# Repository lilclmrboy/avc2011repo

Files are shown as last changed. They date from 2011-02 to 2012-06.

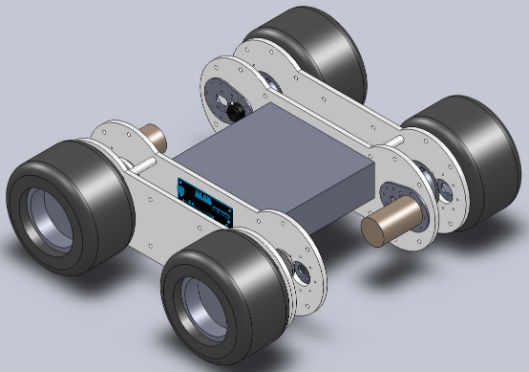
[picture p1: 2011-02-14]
cad/UAV_platform_small.jpg

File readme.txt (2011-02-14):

##########################################################################
# Readme.txt file for AVG2011 project

Download Acroname product sources and integrate the SVN repository. 
Aka, how do I get these files to just work with the download files. 
Launch a terminal session and get to it. 

1.) Move into a directory that you just downloaded the files from Acroname.
2.) Copy the files into your avc2011repo directory

$ cp -Rv acroname/ /Users/you/avc2011rep/source

That should be it. Get working!

##########################################################################
# TEAWare information
# Getting the Stem files ready for deployment to the Stem network

There is a make command to build the project settings for the stem network.

$ make dump

This should create a file to load all the TEAWare onto the Stem network. From the aConsole application:

brainstem> braindump avc2011_dump.dump
wtf

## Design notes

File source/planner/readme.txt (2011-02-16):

Building:
  Currently only builds the release version.
  Requires an acroname directory be a sibling 
  to the examples directory.

Configuration:

Use:

Known Issues:

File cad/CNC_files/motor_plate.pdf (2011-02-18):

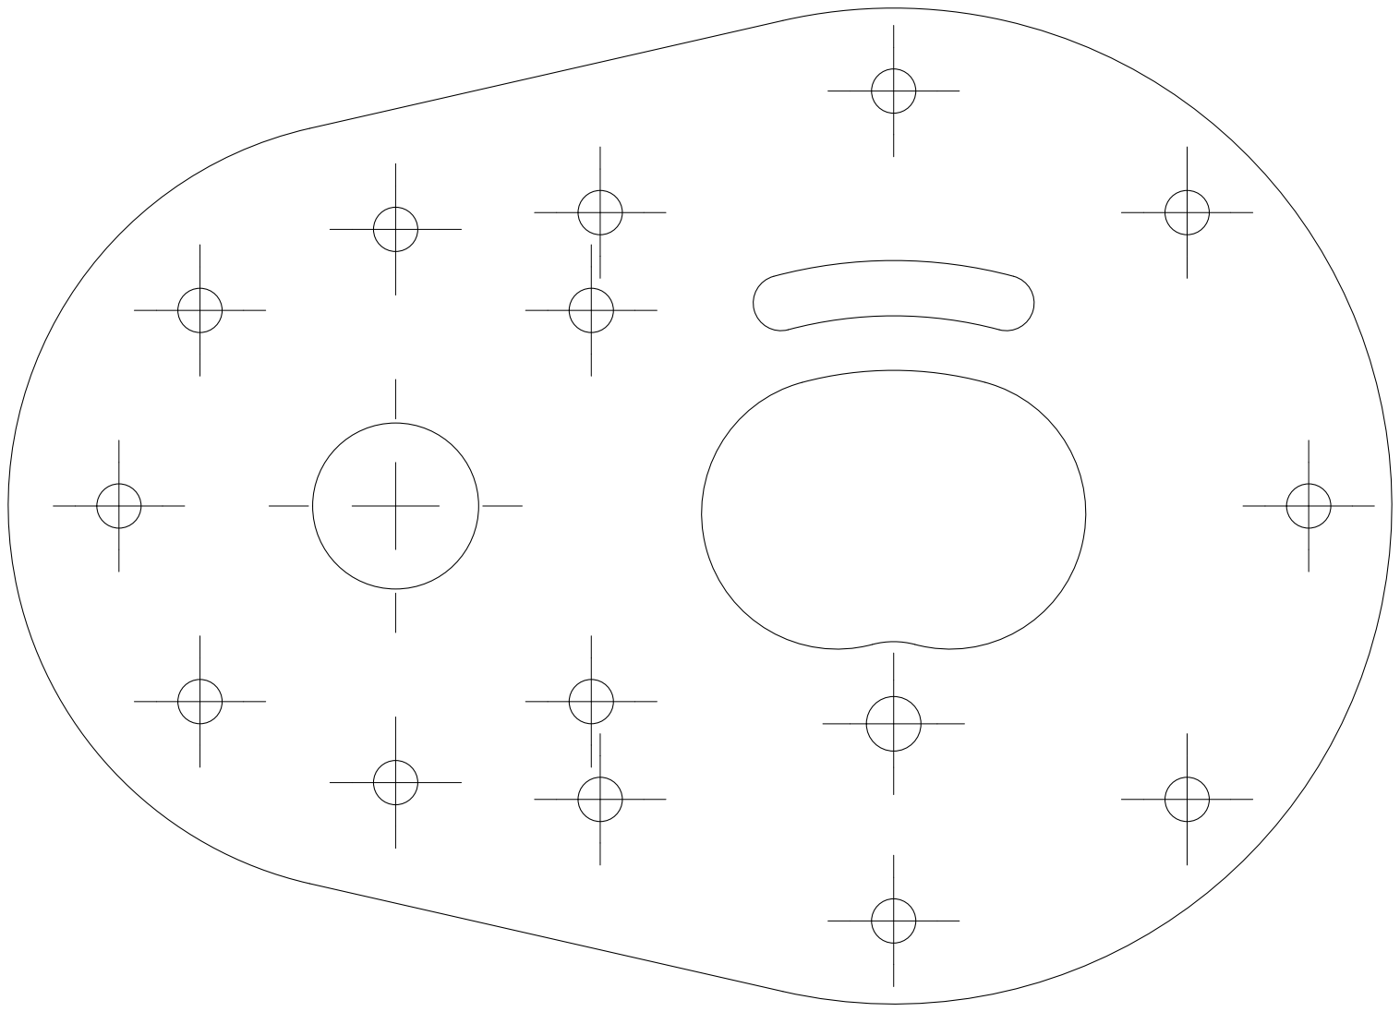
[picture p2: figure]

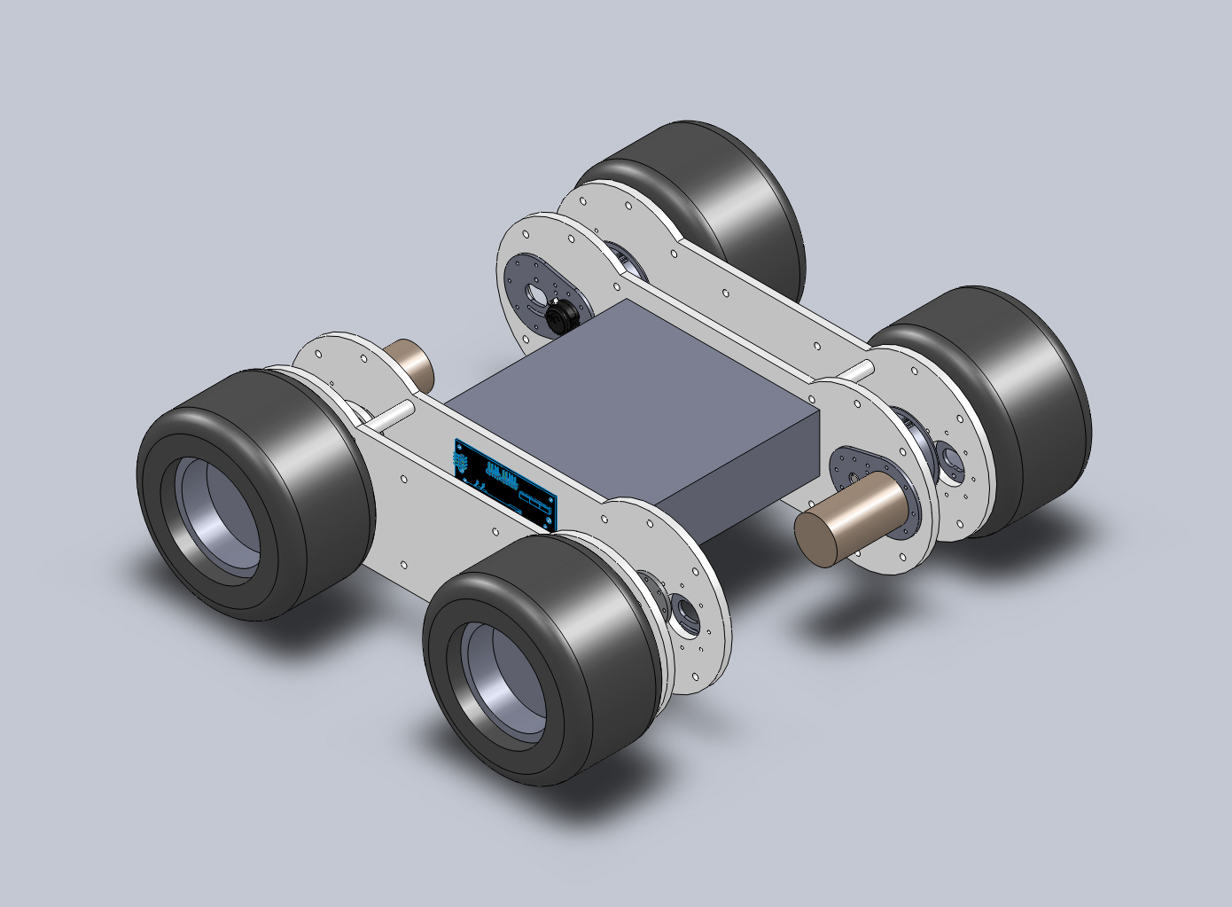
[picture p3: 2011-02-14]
cad/UAV_platform.JPG

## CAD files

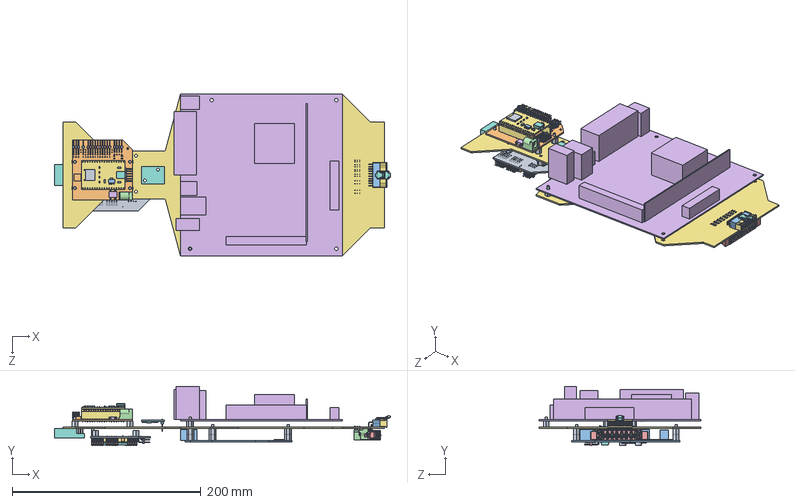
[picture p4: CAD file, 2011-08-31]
cad/avc2012/PCB_Plate_Subsystem.SLDASM
355.8 x 62.8 x 171.4 mm
nylon_standoff_0.25 x 14
BrainStem_Breakout_Eval1
PCONN00009 x 2
PCONN00016
PCONN00027 x 4
TSW-104-08-G-D-RA
SSW-118-01-G-S x 2
TSW-101-08-G-T-RA
TSW-103-08-G-T-RA
Inductor_DR7 x 2
PDIOD00001 x 4
PDIOD00002 x 4
PDIOD00009 x 3
4SMD
BrainStem_USB_Core
USB-minib
DM3D-SF
TSW-118-07-G-S x 2
SOT-223
Capacitor_SMA x 3
LQFP100
PDIOD00013
S08
AR6115
S25-GP2-BRD
PDIOD00003
PCONN00008
PCONN00003
PCONN00012
PCONN00011
PDIPSocket14 x 2
PDIP28
Capacitor_Panasonic_FK_D x 2
PMISC00005
Belkin_F7D1301v1
Samtec-SSW-109-01-G-S
MPSS-08-SR-END
xc-179-xx-x-xx_Crimped x 20
IPD1-XX-D-X-X_6 Position -R
LTC-14-XX-X_-01
T-1S64-XX-X_-09 -RA [IPL1] x 10
T-1S64-XX-X_-10 -RA [IPL1] x 10
IPL1-XX-D-X-XX_No Pol Formula
ced-MPT-XX-RA-XX-XX_8p-SD
ced-T-1M40-XX-X_-02 (.093 PCB) x 8
miniITX
PCB_Plate
R340-CMPS09

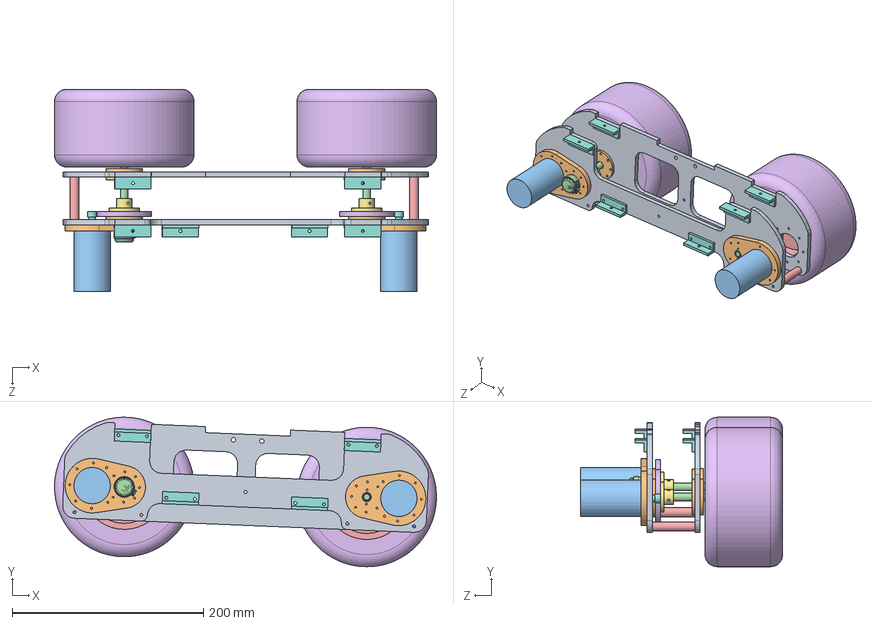
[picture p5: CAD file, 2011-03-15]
cad/Right_Half_Assembly.SLDASM
399.8 x 156.5 x 211.8 mm
Side_Plates2
motor_plate2 x 6
skate_bearing x 4
wheel_shaft x 2
wheel_hub x 2
tire x 2
shaft_hex_connector x 2
angle_supports x 6
Side_Plates2_itx_cutout
motor_plate x 2
titan_550_motor x 2
E4P-X-059-X-D-D-X
spacer x 2
traxxas_32_Pitch_72T_Spur_Gear x 2
traxxas_Spur_Gear_Hub x 2
traxxas_32_Pitch_12T_pINION_Gear x 2

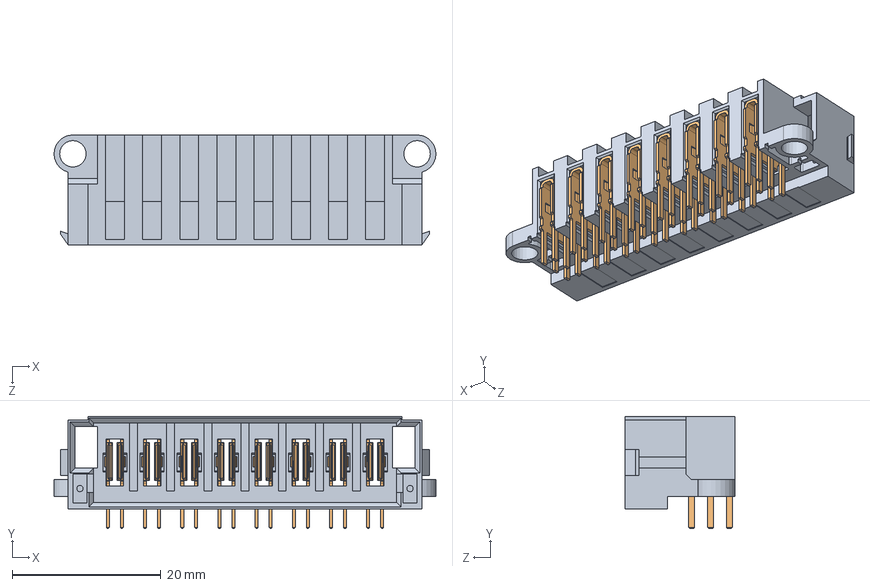
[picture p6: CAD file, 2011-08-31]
cad/avc2012/MPT-08-01-01-X-RA-SD.SLDASM
51.4 x 15.1 x 14.8 mm
ced-MPT-XX-RA-XX-XX_8p-SD
ced-T-1M40-XX-X_-02 (.093 PCB) x 8

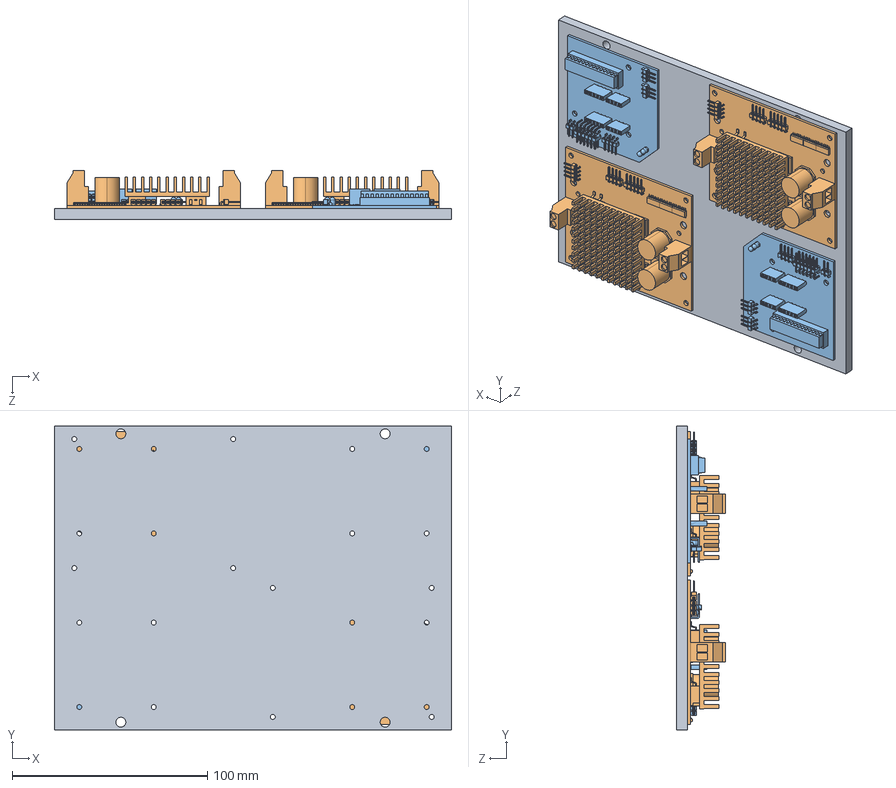
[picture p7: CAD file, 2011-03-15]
cad/bottom_electronics_assembly.SLDASM
203.2 x 155.6 x 25.2 mm
bottom_electronics_plate
S24-15A-30V-HBRIDGE_2010 x 2
S10-MOTO-BRD_2010 x 2

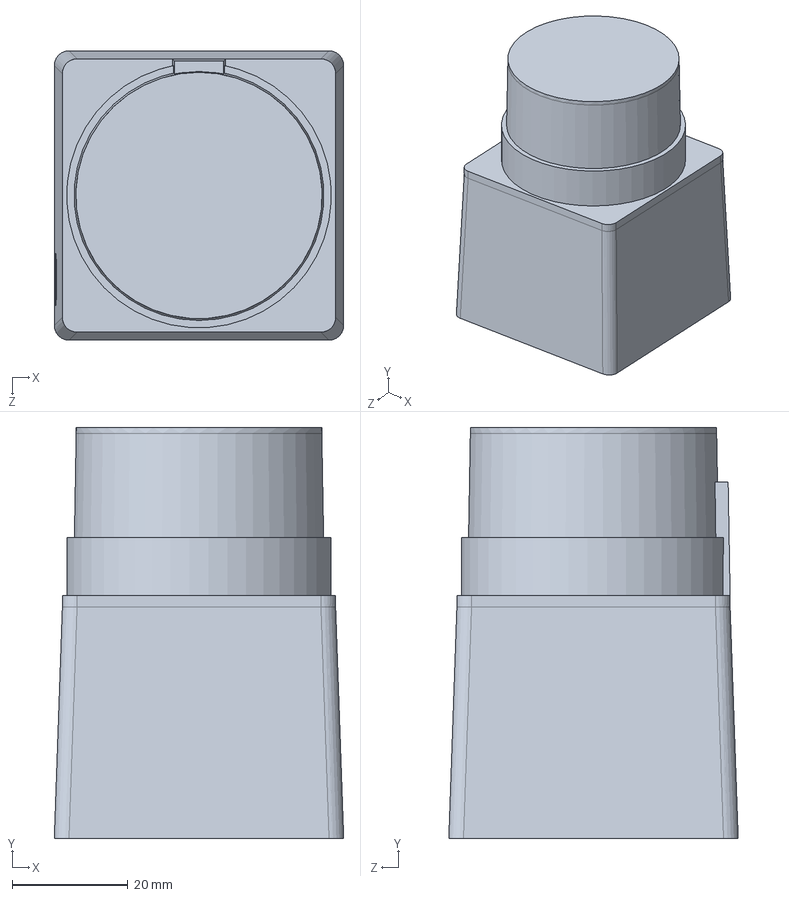
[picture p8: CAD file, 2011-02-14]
cad/SW_2010_files/URG-04LX-UG01_2010.SLDASM
50.0 x 71.0 x 50.0 mm
R325-URG-04LX-UG01
USB-minib

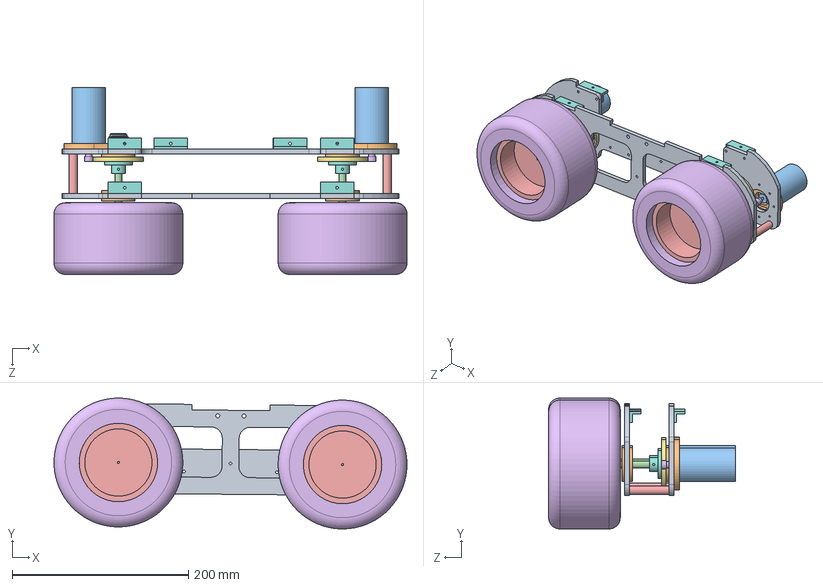
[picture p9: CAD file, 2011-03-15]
cad/Left_Half_Assembly.SLDASM
400.0 x 148.3 x 211.8 mm
Side_Plates2
motor_plate2 x 6
skate_bearing x 4
wheel_shaft x 2
wheel_hub x 2
tire x 2
shaft_hex_connector x 2
angle_supports x 6
Side_Plates2_itx_cutout
motor_plate x 2
titan_550_motor x 2
E4P-X-059-X-D-D-X
spacer x 2
traxxas_32_Pitch_12T_pINION_Gear x 2
traxxas_32_Pitch_72T_Spur_Gear x 2
traxxas_Spur_Gear_Hub x 2

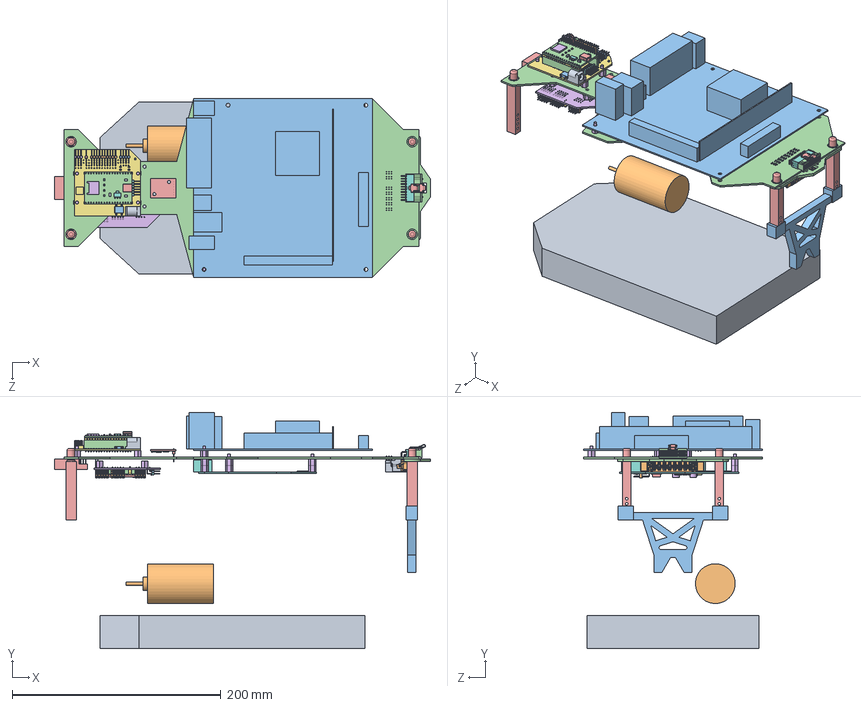
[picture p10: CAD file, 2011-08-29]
cad/avc2012/avc2012.SLDASM
360.5 x 226.6 x 171.4 mm
nylon_standoff_0.25 x 14
BrainStem_Breakout_Eval1
PCONN00009 x 2
PCONN00016
PCONN00027 x 4
TSW-104-08-G-D-RA
SSW-118-01-G-S x 2
TSW-101-08-G-T-RA
TSW-103-08-G-T-RA
Inductor_DR7 x 2
PDIOD00001 x 4
PDIOD00002 x 4
PDIOD00009 x 3
4SMD
BrainStem_USB_Core
USB-minib
DM3D-SF
TSW-118-07-G-S x 2
SOT-223
Capacitor_SMA x 3
LQFP100
PDIOD00013
S08
AR6115
S25-GP2-BRD
PDIOD00003
PCONN00008
PCONN00003
PCONN00012
PCONN00011
PDIPSocket14 x 2
PDIP28
Capacitor_Panasonic_FK_D x 2
PMISC00005
Belkin_F7D1301v1
Samtec-SSW-109-01-G-S
MPSS-08-SR-END
xc-179-xx-x-xx_Crimped x 20
IPD1-XX-D-X-X_6 Position -R
LTC-14-XX-X_-01
T-1S64-XX-X_-09 -RA [IPL1] x 10
T-1S64-XX-X_-10 -RA [IPL1] x 10
IPL1-XX-D-X-XX_No Pol Formula
ced-MPT-XX-RA-XX-XX_8p-SD
ced-T-1M40-XX-X_-02 (.093 PCB) x 8
miniITX
PCB_Plate
R340-CMPS09

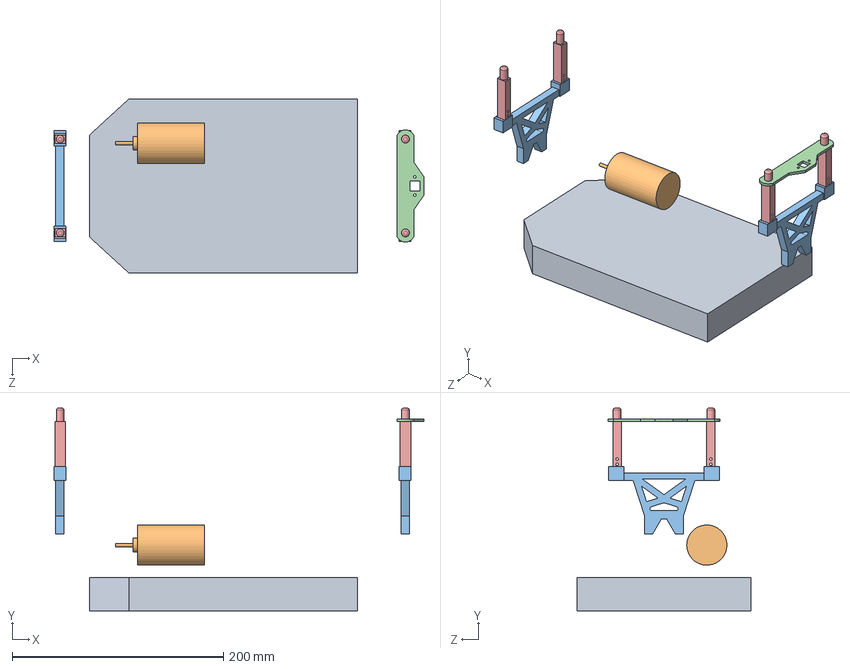
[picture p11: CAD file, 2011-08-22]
cad/avc2012/Traxxas_EMAXX.SLDASM
350.5 x 192.1 x 165.1 mm
Traxxas_EMAXX_Cavity
titan_550_motor
Traxxas_EMAXX_PostBrace x 2
Traxxas_EMAXX_RearPostMount
Traxxas_EMAXX_Post x 4

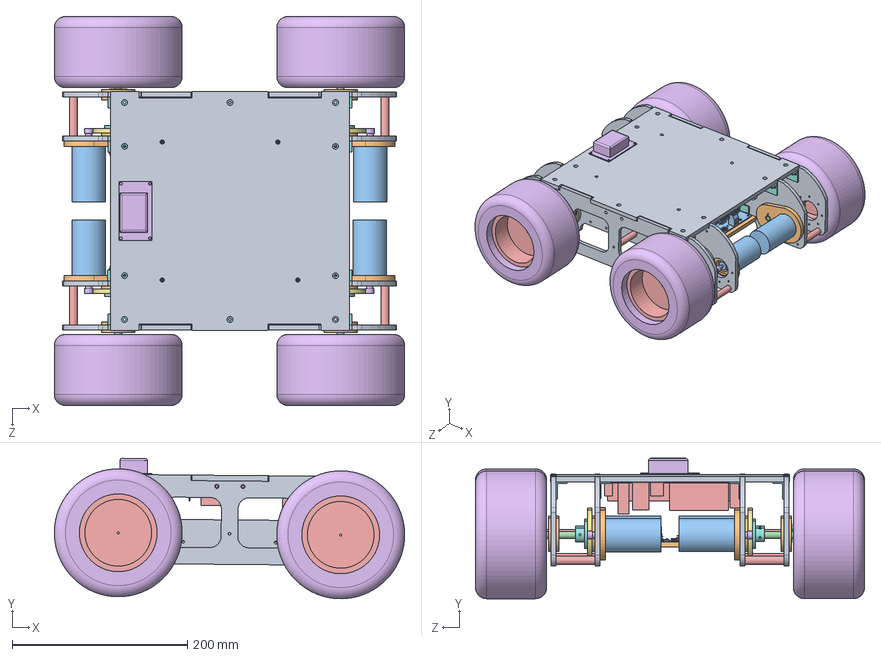
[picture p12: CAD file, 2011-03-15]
cad/UAV_platform3.SLDASM
400.0 x 160.4 x 444.1 mm
Side_Plates2 x 2
motor_plate2 x 12
skate_bearing x 8
wheel_shaft x 4
wheel_hub x 4
tire x 4
shaft_hex_connector x 4
angle_supports x 14
Side_Plates2_itx_cutout x 2
motor_plate x 4
titan_550_motor x 4
E4P-X-059-X-D-D-X x 2
spacer x 6
traxxas_32_Pitch_12T_pINION_Gear x 4
traxxas_32_Pitch_72T_Spur_Gear x 4
traxxas_Spur_Gear_Hub x 4
top_electronic_plate
bottom_electronics_plate
S24-15A-30V-HBRIDGE_2010 x 2
S10-MOTO-BRD_2010 x 2
miniITX
DS-GPMu_2010

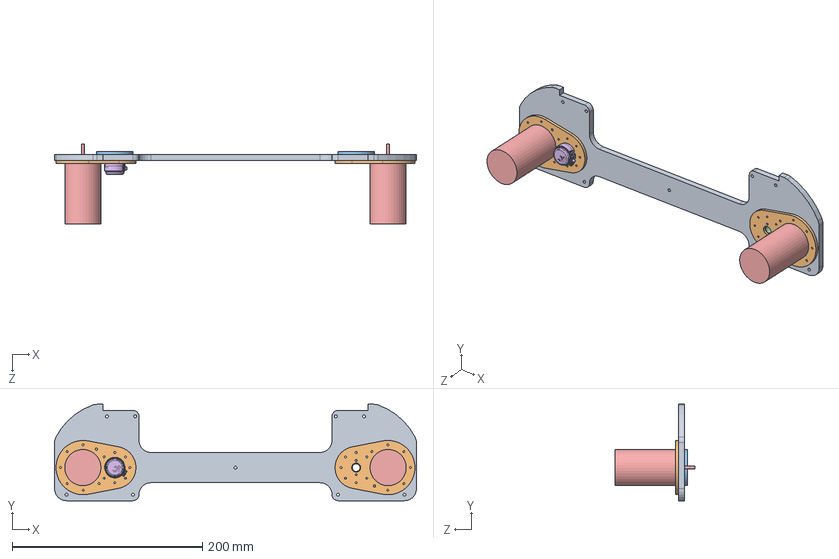
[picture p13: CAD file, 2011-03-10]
cad/Right_Side_Plate_Assembly.SLDASM
381.0 x 101.6 x 84.1 mm
Side_Plates2_itx_cutout
motor_plate x 2
motor_plate2 x 2
skate_bearing x 2
titan_550_motor x 2
E4P-X-059-X-D-D-X

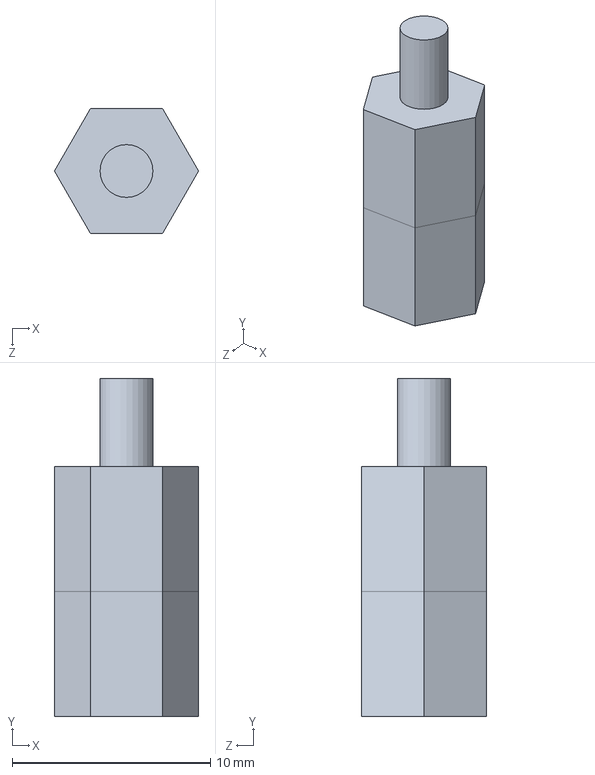
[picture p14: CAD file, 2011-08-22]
cad/avc2012/Nylon_standoff_0.5.SLDASM
7.27 x 17.0 x 6.30 mm
nylon_standoff_0.25 x 2

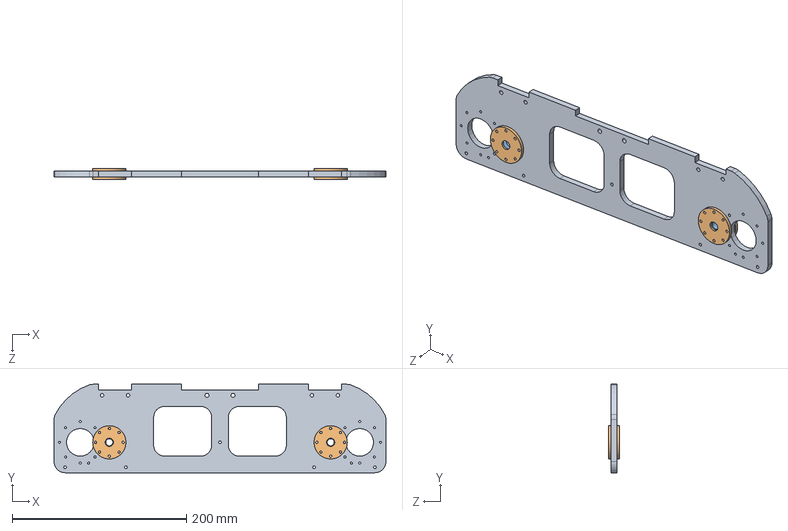
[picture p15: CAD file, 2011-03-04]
cad/Side_Plate_Assembly4_no_motor.SLDASM
381.0 x 101.6 x 12.7 mm
Side_Plates2
motor_plate2 x 4
skate_bearing x 2

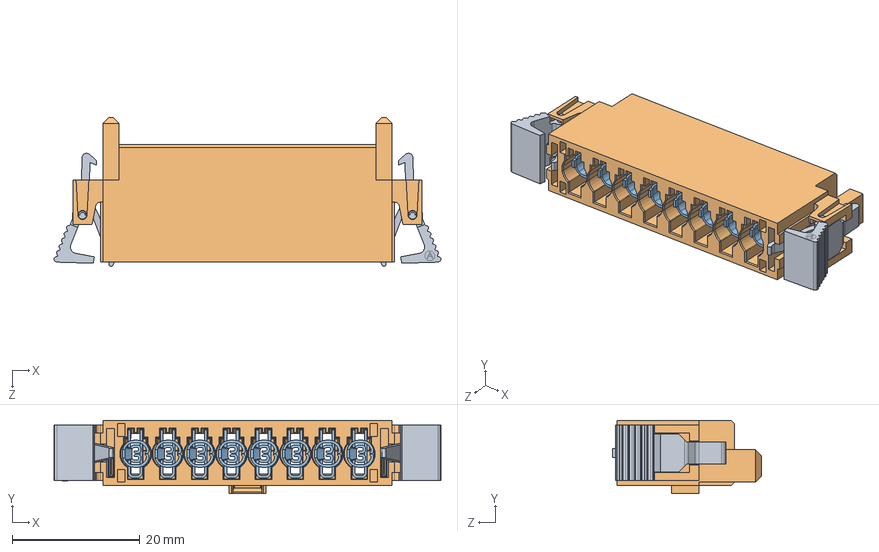
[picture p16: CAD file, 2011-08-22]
cad/avc2012/MPSS-08-SR-END.SLDASM
60.6 x 11.4 x 23.3 mm
LTC-22 x 2
MPSS-XX-R-XX
C-246-XX-X_14 Gauge Crimped x 8

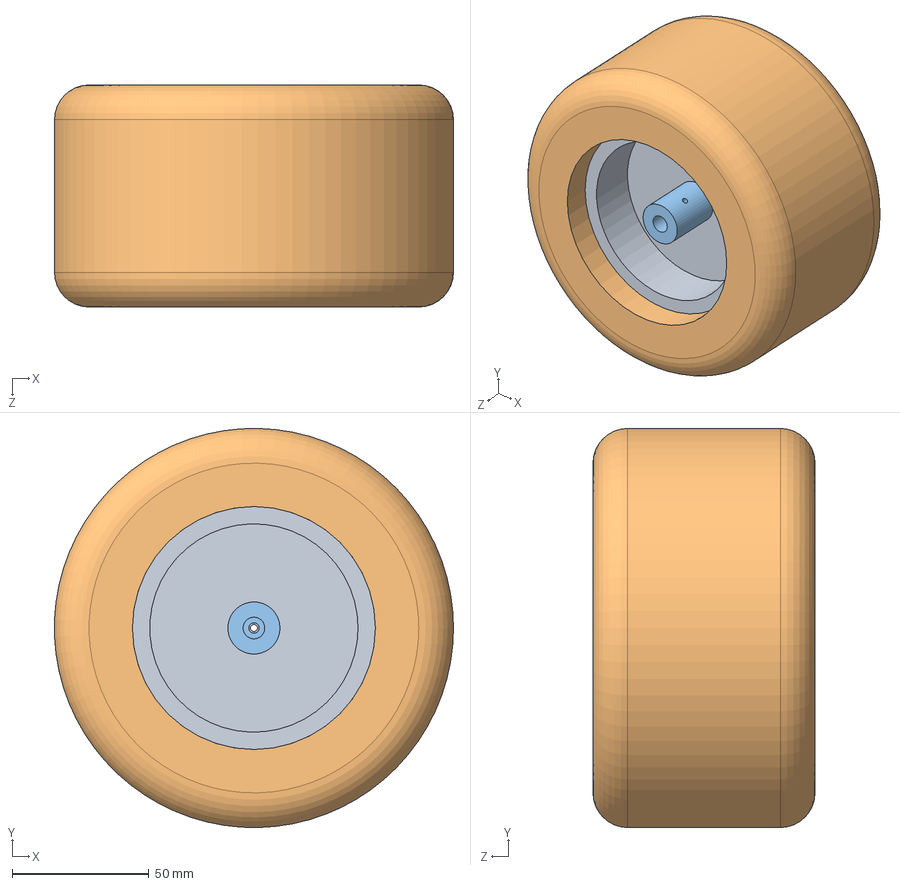
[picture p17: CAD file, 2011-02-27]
cad/wheel_Assembly.SLDASM
146.0 x 146.0 x 81.3 mm
wheel_hub
tire
shaft_hex_connector

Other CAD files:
cad/Left_Side_Plate_Assembly.SLDASM
cad/traxxas_Spur_Gear_wHub.SLDASM
cad/Side_Plate_Assembly_Right.SLDASM
cad/Side_Plate_Assembly3.SLDASM
cad/A 6H 3-34DF03710.SLDPRT
cad/BQ24703EVM.IGS
cad/BQ24703EVM.SLDPRT
cad/CNC_files/motor_plate.DXF
cad/CNC_files/motor_plate2.DXF
cad/CNC_files/motor_plate2_jig.dwg
cad/CNC_files/motor_plate_cnc.dxf
cad/CNC_files/motor_plate_outline.dxf
cad/CNC_files/shaft_hex_connector.DXF
cad/DS-GPMu.IGS
cad/DS-GPMu.SLDPRT
cad/E4P-X-059-X-D-D-X.SLDPRT
cad/GM9234S022.IGS
cad/GM9234S022.SLDPRT
cad/Hub_threaded_side.SLDPRT
cad/ITX_CPU.SLDPRT
cad/R323-ME-110.IGS
cad/R323-ME-110.SLDPRT
cad/R340-CMPS09.IGS
cad/R340-CMPS09.SLDPRT
cad/RRR_48_Pitch_96T_Spur_Gear.SLDPRT
cad/S10-MOTO-BRD.SLDPRT
cad/S24-15A-30V-HBRIDGE.SLDPRT
cad/S25-GP2-BRD.SLDPRT
cad/SW_2010_files/BQ24703EVM_2010.SLDPRT
cad/SW_2010_files/DS-GPMu_2010.SLDPRT
cad/SW_2010_files/R340-CMPS09_2010.SLDPRT
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

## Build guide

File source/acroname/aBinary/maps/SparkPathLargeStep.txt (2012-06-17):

-105.2100908507309,40.0652253094504,90
-105.2098240103828,40.06520983138007,90
-105.2097629026131,40.06518667392859,135
-105.2097308279193,40.06513177912552,180
-105.209738150582,40.06491557682288,180
-105.2097501444705,40.06452415012394,180
-105.2097884312028,40.0644668854269,270
-105.2099424715226,40.06447739617511,270
-105.2104200633587,40.06451314122317,270
-105.2104465821731,40.06461422852355,0
-105.2104270199432,40.06521965594927,0
-105.2102729670725,40.06524202265999,90
-105.2100574241598,40.06524855372022,90

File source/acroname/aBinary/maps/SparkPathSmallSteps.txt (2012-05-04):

-105.2099849376928,40.06523891649416,0
-105.2099747180741,40.06523893440954,0
-105.2099508701032,40.06523897615521,0
-105.2099372413914,40.06523899994227,0
-105.2099167962623,40.06523903575222,0
-105.2099065728328,40.06523905363946,0
-105.2098793154115,40.06523911741146,0
-105.209858850937,40.06523390802446,0
-105.2098486365671,40.06523395287834,0
-105.2098315923857,40.06523137764867,0
-105.2098213747526,40.06523142221354,0
-105.2097975132334,40.0652288763124,0
-105.2097872491586,40.06522097178065,0
-105.2097769740989,40.06521042107813,0
-105.2097735278175,40.06520249277323,0
-105.2097700590067,40.06518928284276,0
-105.2097665800996,40.06517343862516,0
-105.2097597246912,40.0651629002795,0
-105.2097596814555,40.06515495525525,0
-105.2097562030686,40.06514172354965,0
-105.2097561154387,40.06512585140557,0
-105.2097560433619,40.06511263893394,0
-105.2097559862098,40.06510207717425,0
-105.2097559006371,40.0650862465189,0
-105.209755852504,40.06507572319551,0
-105.2097558199288,40.06506264351676,0
-105.2097557874401,40.06504956843143,0
-105.2097557484379,40.06503388422148,0
-105.2097557155511,40.06502081821273,0
-105.2097488925166,40.06500776335197,0
-105.2097488462483,40.06499207759749,0
-105.2097454175225,40.06497902248123,0
-105.209745387332,40.0649685739176,0
-105.2097453420211,40.06495290770764,0
-105.2097453042896,40.0649398585749,0
-105.2097452741859,40.06492942333718,0
-105.2097452289247,40.06491377697133,0
-105.2097451912405,40.06490074440278,0
-105.2097451611222,40.06489032235529,0
-105.2097451121178,40.06487468983899,0
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

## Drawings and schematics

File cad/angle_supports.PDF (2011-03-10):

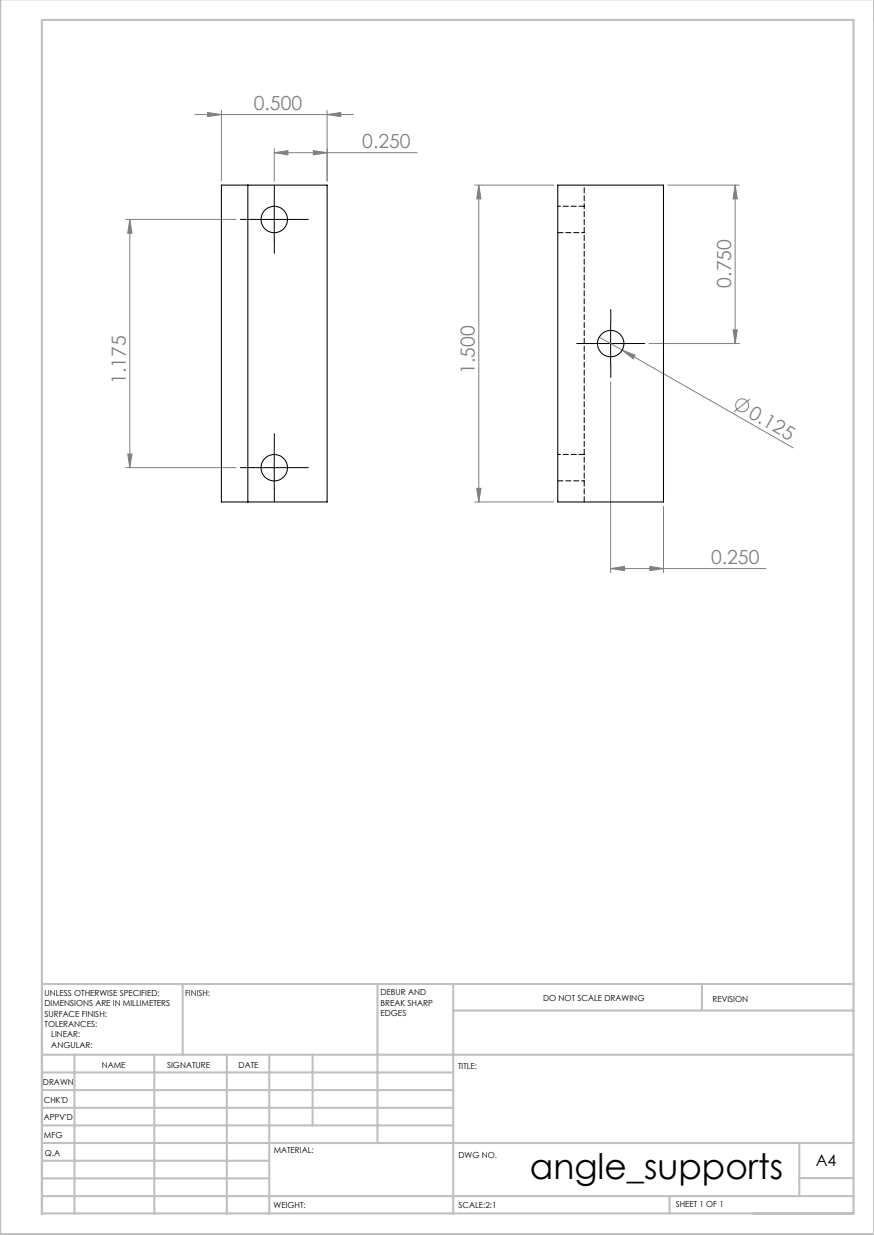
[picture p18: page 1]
SCALE:2:1; SHEET 1 OF 1; DO NOT SCALE DRAWING; REVISION; DEBUR AND BREAK SHARP; UNLESS OTHERWISE SPECIFIED:; FINISH:

DIMENSIONS ARE IN MILLIMETERS
SURFACE FINISH:
TOLERANCES:
LINEAR:
ANGULAR:

NAME | SIGNATURE | DATE | | | | TITLE:
Q.A | | | | MATERIAL: | angle_supports WEIGHT: DWG NO. | A4

DRAWN
CHK'D
APPV'D
MFG

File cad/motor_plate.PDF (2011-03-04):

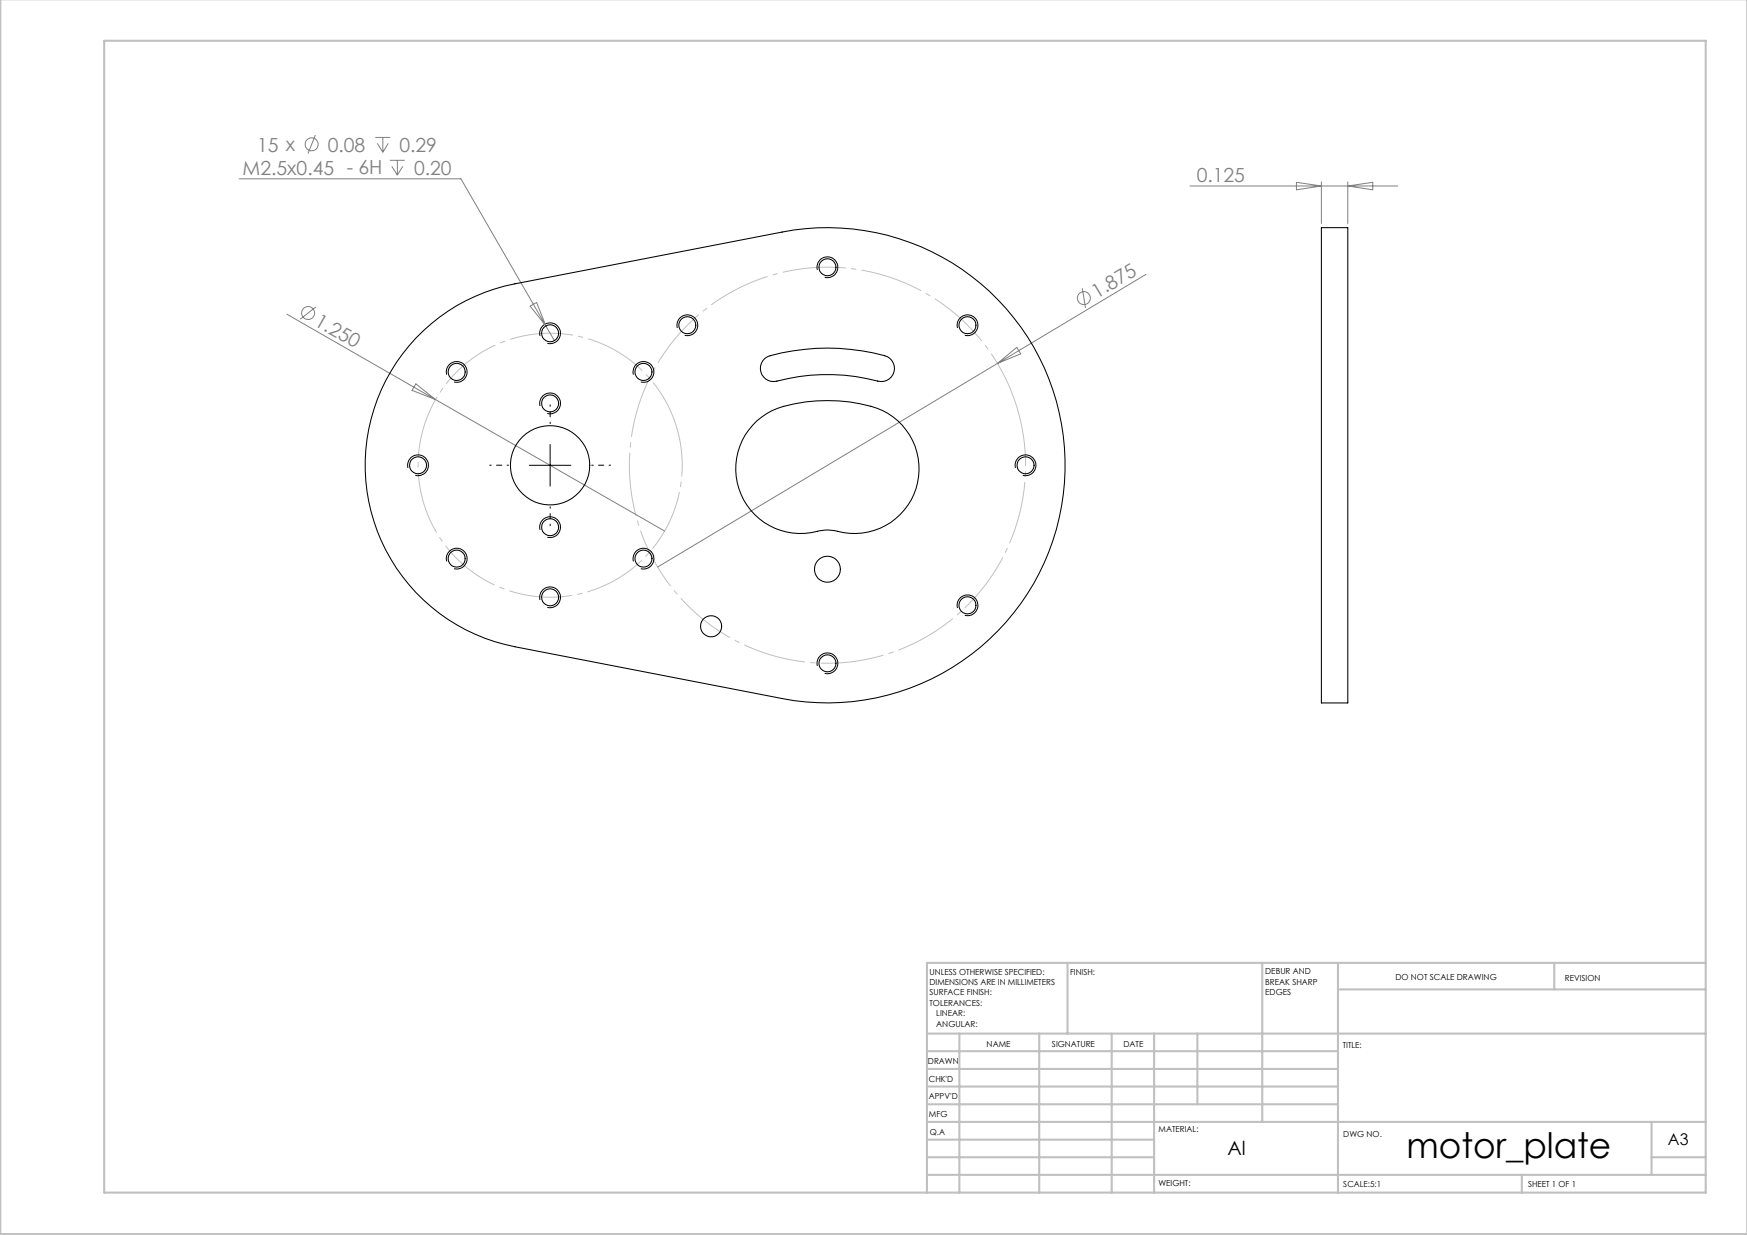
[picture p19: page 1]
SCALE:5:1; SHEET 1 OF 1; DO NOT SCALE DRAWING; REVISION; DEBUR AND BREAK SHARP; UNLESS OTHERWISE SPECIFIED:; FINISH:

DIMENSIONS ARE IN MILLIMETERS
SURFACE FINISH:
TOLERANCES:
LINEAR:
ANGULAR:

NAME | SIGNATURE | DATE | | | | TITLE:
Q.A | | | | MATERIAL: Al | motor_plate WEIGHT: DWG NO. | A3

DRAWN
CHK'D
APPV'D
MFG

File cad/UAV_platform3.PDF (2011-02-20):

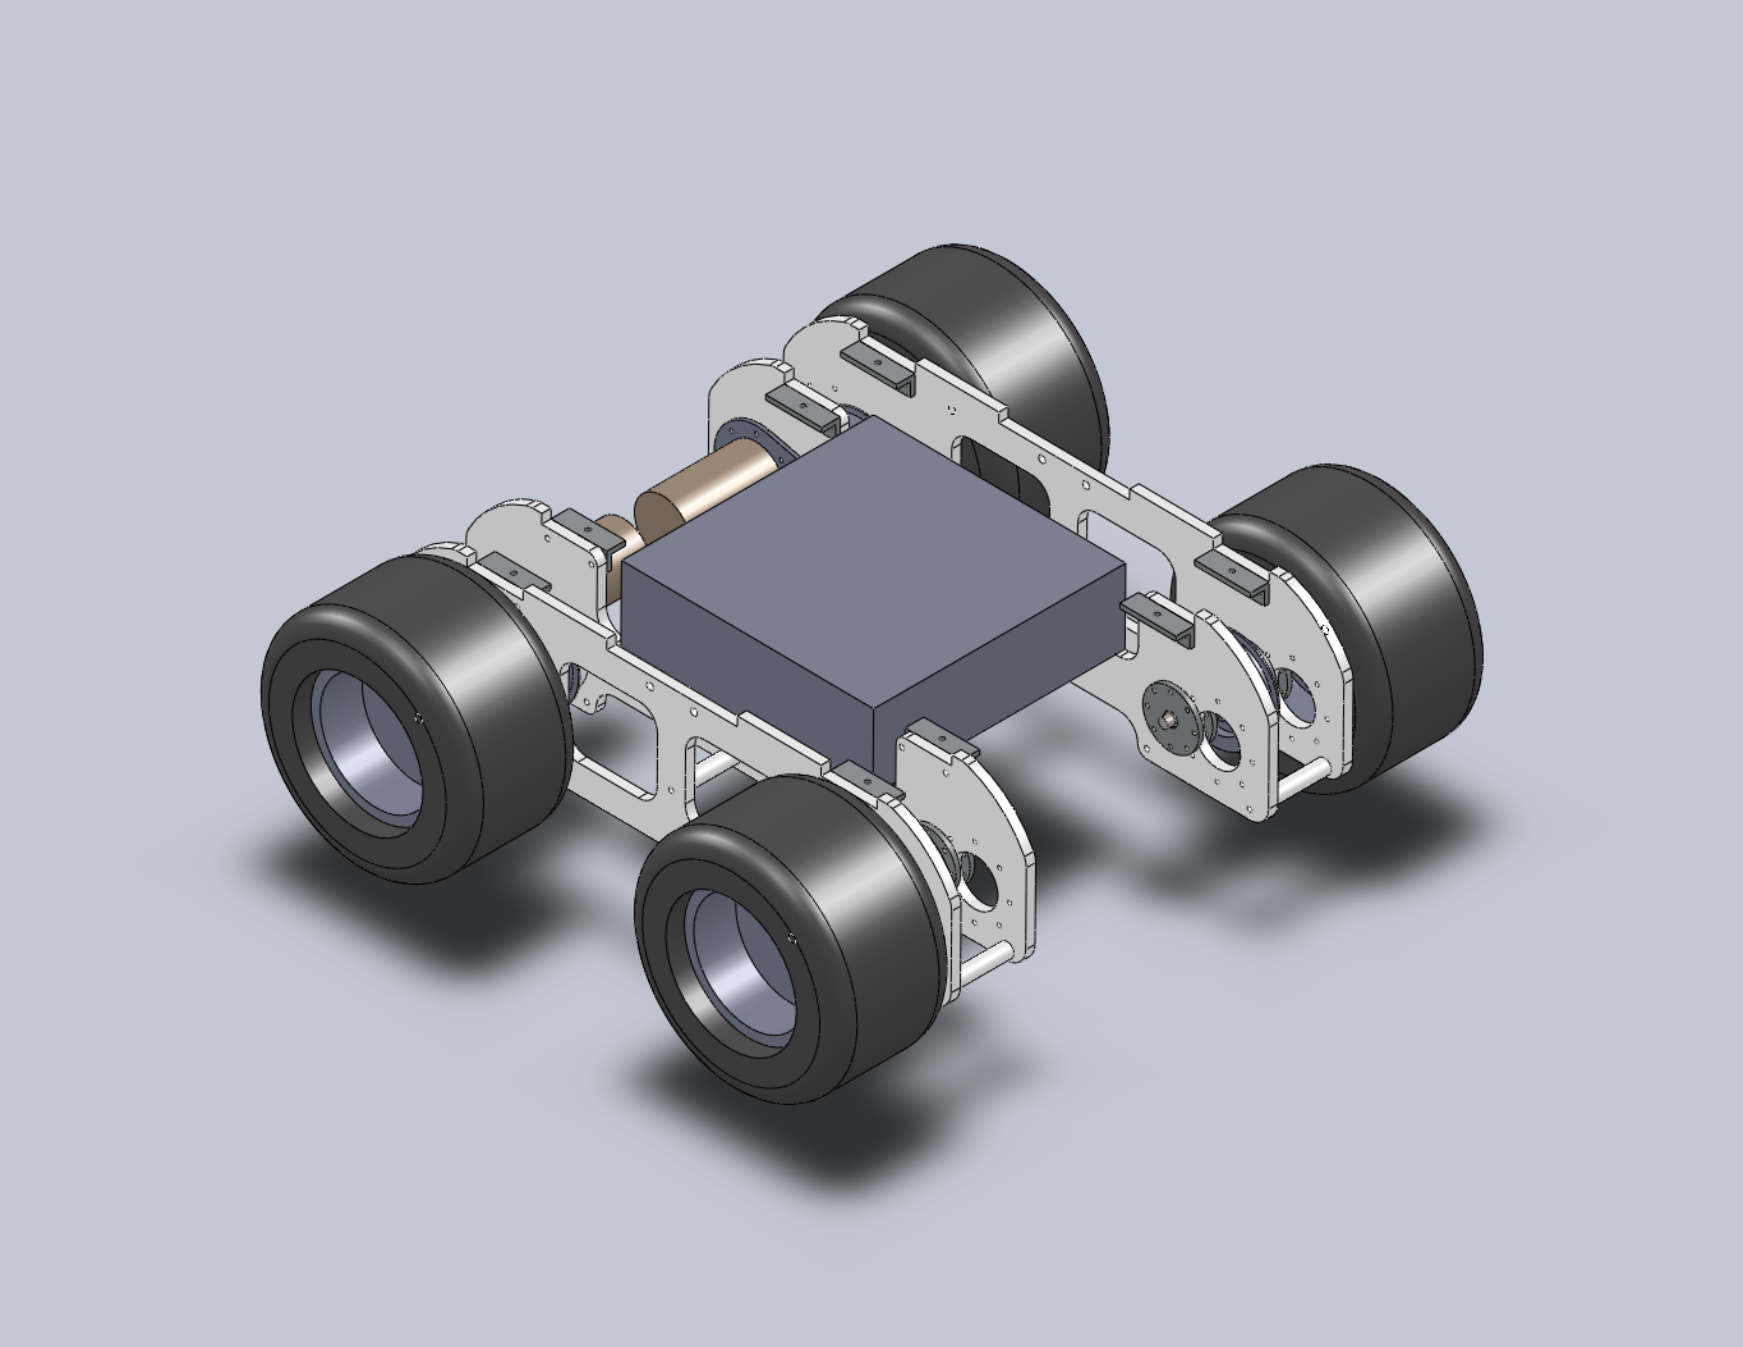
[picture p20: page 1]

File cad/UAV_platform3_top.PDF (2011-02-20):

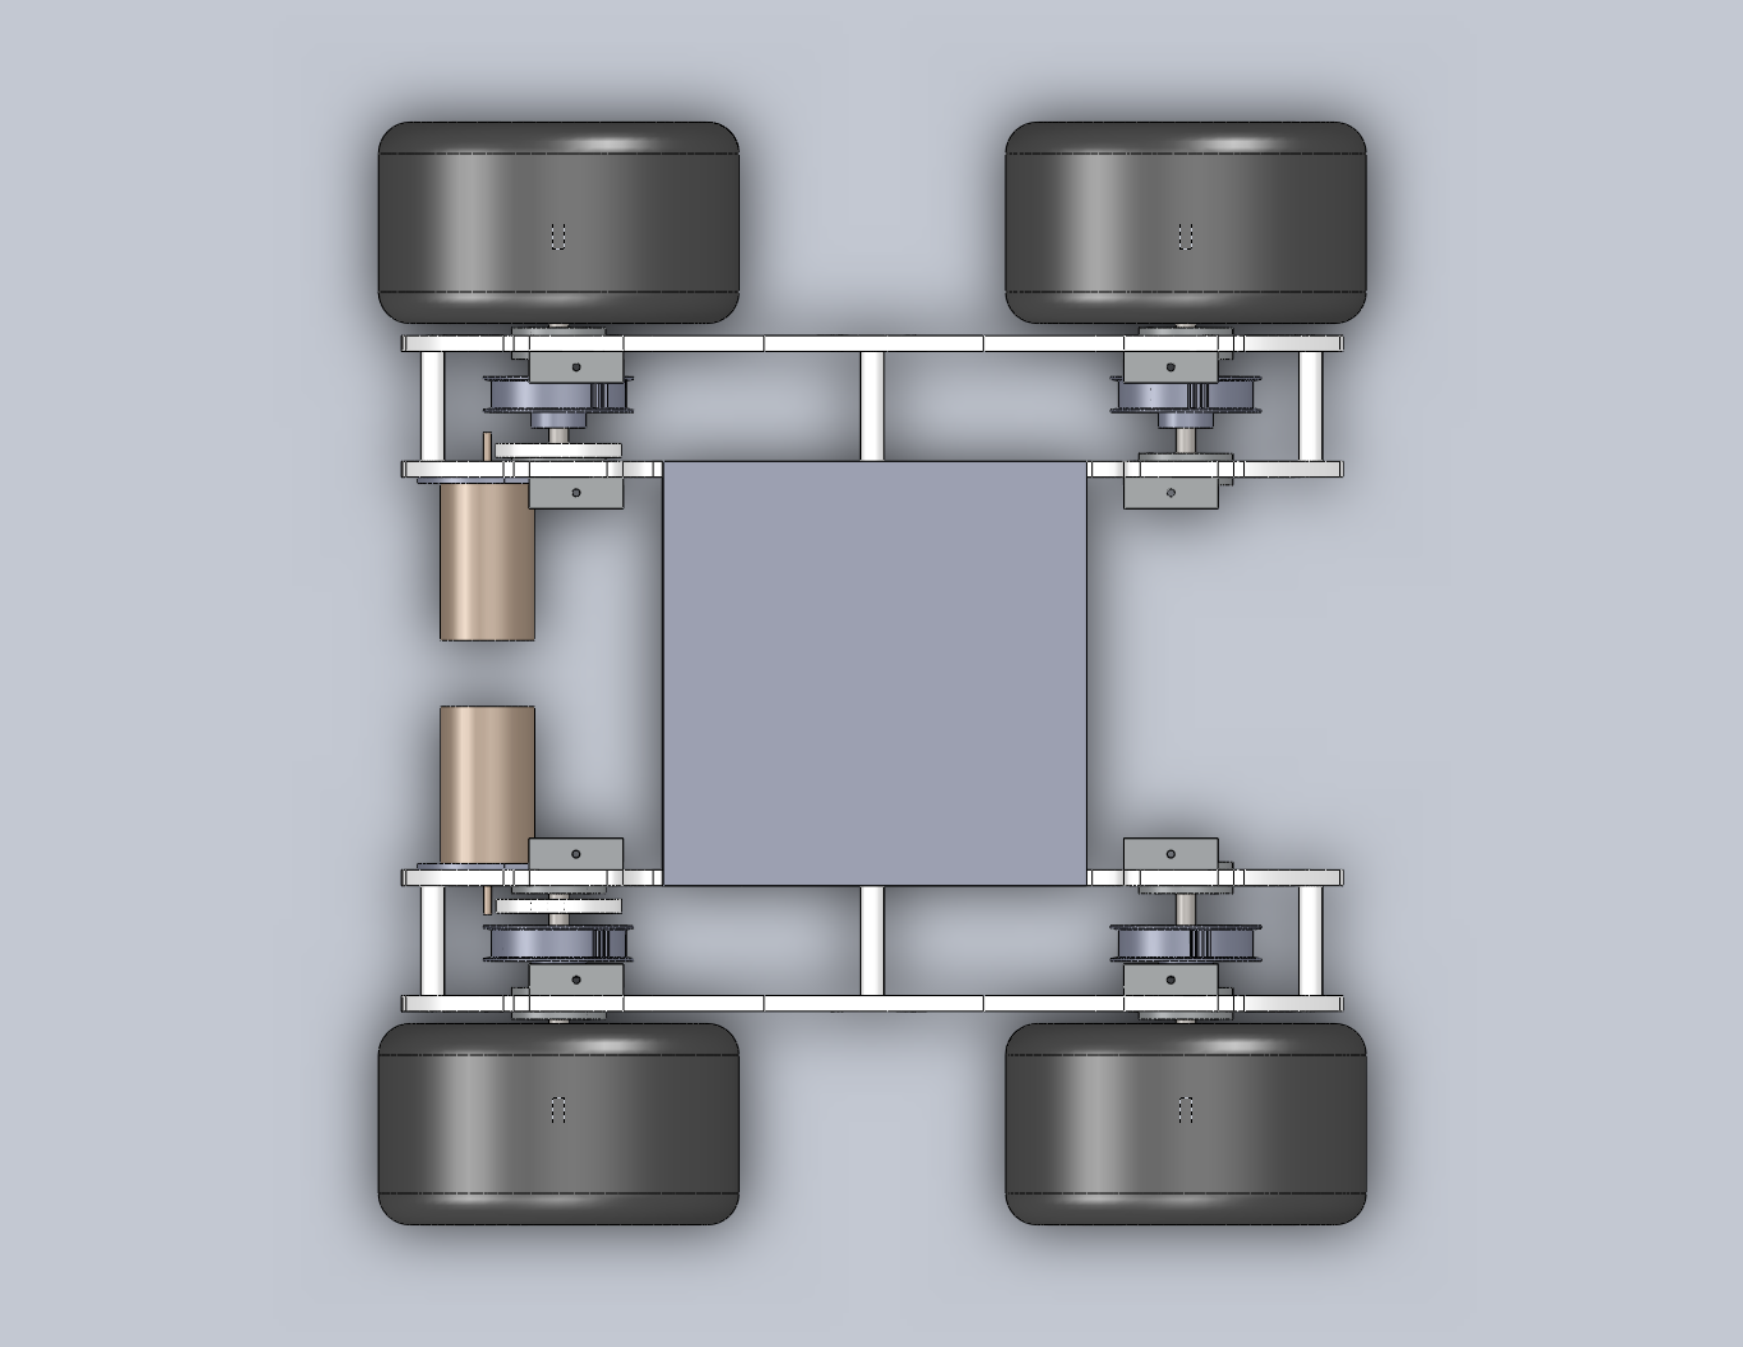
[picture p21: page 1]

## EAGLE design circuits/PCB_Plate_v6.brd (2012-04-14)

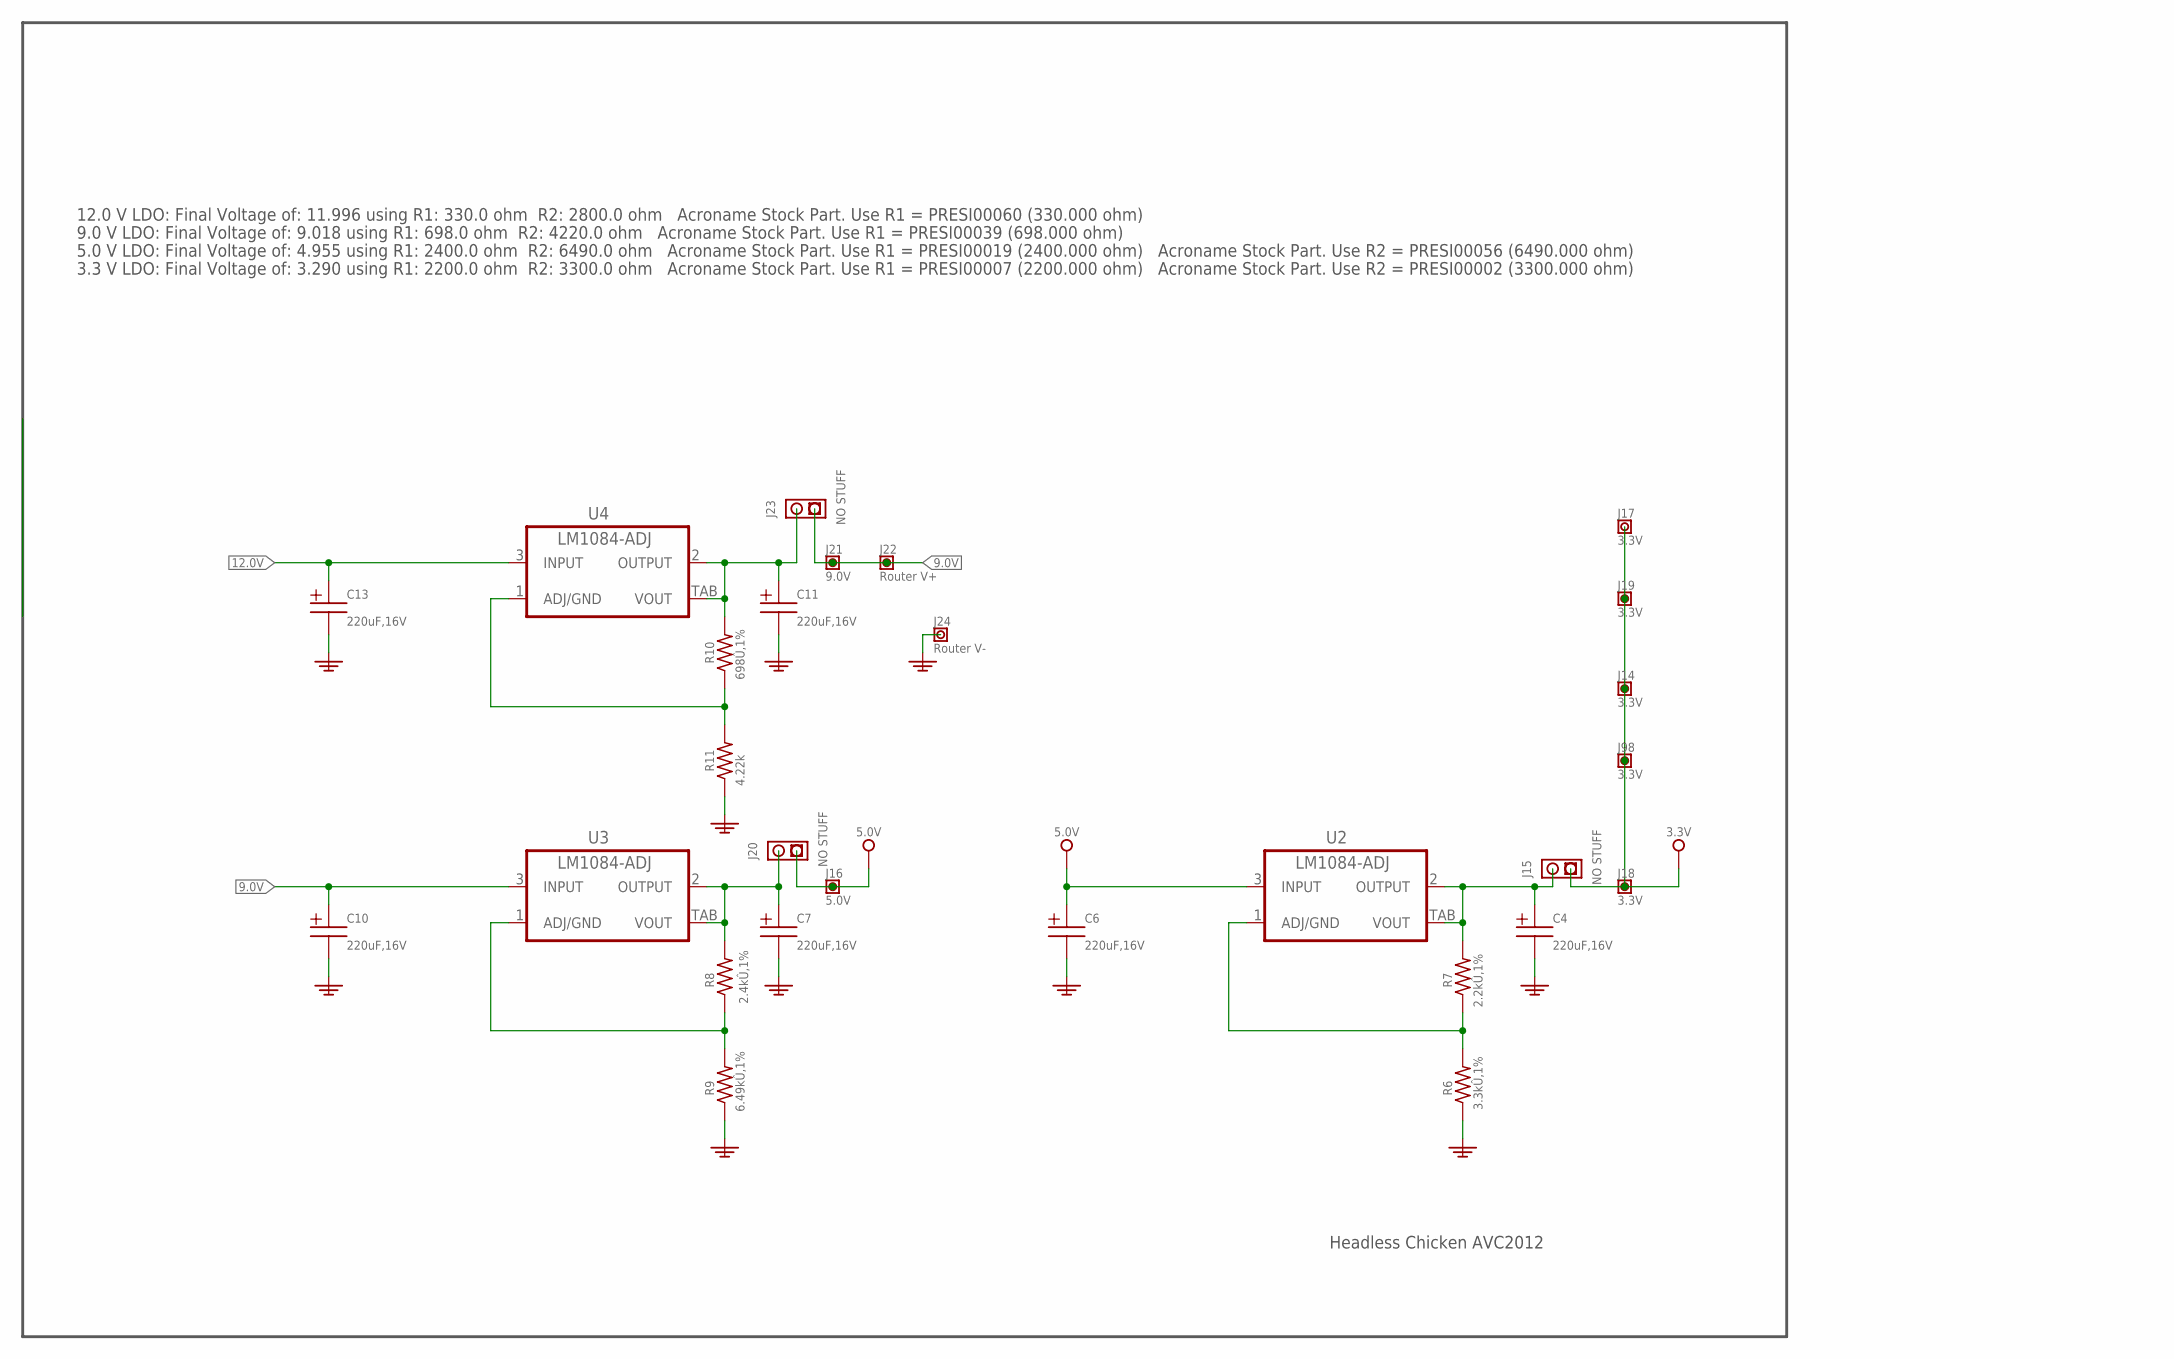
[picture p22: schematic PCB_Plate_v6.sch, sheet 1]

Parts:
C4, C6, C7, C10, C11, C13: T491D227K016ZT; SMC_D
J14, J17, J18, J19, J98: 3.3V; TSW1X1_VAL
J15, J20, J23: BOARD00012; TSW1X2
J16: 5.0V; TSW1X1_VAL
J21: 9.0V; TSW1X1_VAL
J22: Router V+; TSW1X1_VAL
J24: Router V-; TSW1X1_VAL
R6: on; R0603; PARTNUM ERJ-3GEYJ332V
R7: PRESI00007; R0603; PARTNUM ERJ-3GEYJ222V
R8: PRESI00019; R0603; PARTNUM ERJ-3EKF2431V
R9: on; R0402; PARTNUM ERJ-3EKF6491V
R10: PRESI00039; R0603; PARTNUM ERJ-3EKF6980V
R11: on; R0603
U2, U3, U4: LM1084IS-ADJ; TO263-3

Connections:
3V3: J14.P$1, J15.P$1, J17.P$1, J18.P$1, J19.P$1, J98.P$1; also elsewhere on the board
5V0: C6.+, J16.P$1, J20.P$1, U2.3 (INPUT); also elsewhere on the board
9.0V: C10.+, J21.P$1, J22.P$1, J23.P$1, U3.3 (INPUT)
12.0V: C13.+, U4.3 (INPUT); also elsewhere on the board
GND: C4.-, C6.-, C7.-, C10.-, C11.-, C13.-, J24.P$1, R6.1, R9.1, R11.1; also elsewhere on the board
unnamed: R10.1, R11.2, U4.1 (ADJ/GND)
unnamed: R8.1, R9.2, U3.1 (ADJ/GND)
unnamed: R6.2, R7.1, U2.1 (ADJ/GND)
unnamed: C7.+, J20.P$2, R8.2, U3.2 (OUTPUT), U3.TAB (VOUT)
unnamed: C11.+, J23.P$2, R10.2, U4.2 (OUTPUT), U4.TAB (VOUT)
unnamed: C4.+, J15.P$2, R7.2, U2.2 (OUTPUT), U2.TAB (VOUT)

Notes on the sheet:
Headless Chicken AVC2012
12.0 V LDO: Final Voltage of: 11.996 using R1: 330.0 ohm R2: 2800.0 ohm Acroname Stock Part. Use R1 = PRESI00060 (330.000 ohm)
9.0 V LDO: Final Voltage of: 9.018 using R1: 698.0 ohm R2: 4220.0 ohm Acroname Stock Part. Use R1 = PRESI00039 (698.000 ohm)
5.0 V LDO: Final Voltage of: 4.955 using R1: 2400.0 ohm R2: 6490.0 ohm Acroname Stock Part. Use R1 = PRESI00019 (2400.000 ohm) Acroname Stock Part. Use R2 = PRESI00056 (6490.000 ohm)
3.3 V LDO: Final Voltage of: 3.290 using R1: 2200.0 ohm R2: 3300.0 ohm Acroname Stock Part. Use R1 = PRESI00007 (2200.000 ohm) Acroname Stock Part. Use R2 = PRESI00002 (3300.000 ohm)

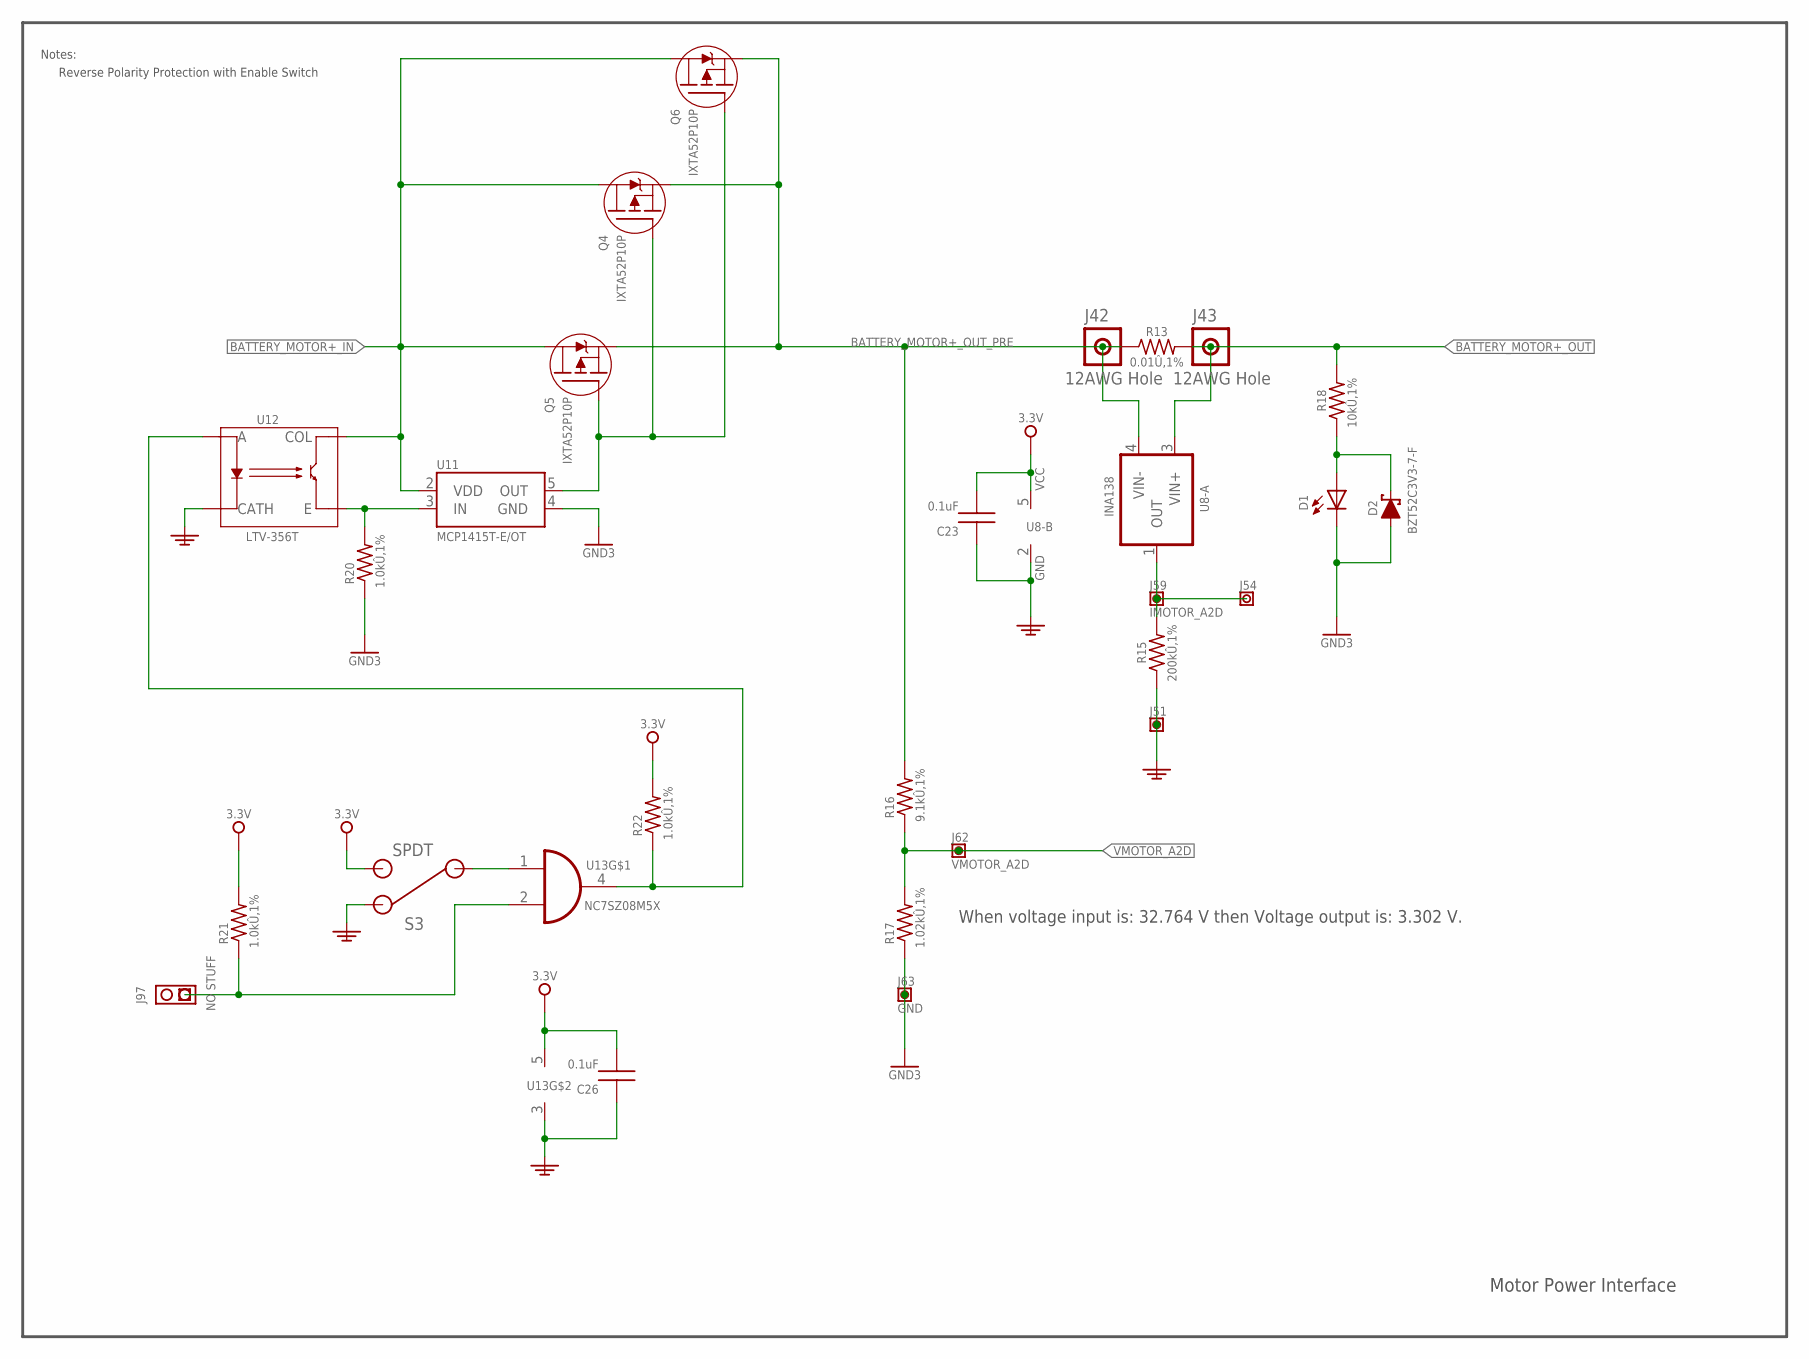
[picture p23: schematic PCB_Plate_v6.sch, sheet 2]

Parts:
C23: PCAPI00015; C0603
C26: PCAPI00015; C0603; PARTNUM ECJ-1VB1E104K
D1: PDIOD00001; CHIPLED_0805
D2: BZT52C3V3-7-F; SOD123
J42, J43: BOARD00008; TSW1X1_12AWG
J51, J54: BOARD00003WVALUE; TSW1X1_VAL
J59: IMOTOR_A2D; TSW1X1_VAL
J62: VMOTOR_A2D; TSW1X1_VAL
J63: GND; TSW1X1_VAL
J97: BOARD00012; TSW1X2
Q4, Q5, Q6: IXTA52P10P; D2PACK
R13: PRESI00041; R4527
R15: PRESI00018; R0603
R16: ERJ-2RKF9101X; R0402@1
R17: ERJ-2RKF1021X; R0402@1
R18: PRESI00005; R0603
R20, R21: PRESI00006; R0603; PARTNUM ERJ-3EKF1001V
R22: PRESI00006; R0603
S3: PMISC00005; SPDTRA
U8: PCHIP00026; SOT23-5
U11: MCP1416; SOT23-5; PARTNUM MCP1415T-E/OT
U12: LTV-356T; 4-SMD
U13: NC7SZ08M5X; SOT23-5

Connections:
3V3: C23.2, C26.2, R21.2, R22.2, S3.3 (2), U8.5 (VCC), U13.5 (VCC); also elsewhere on the board
BATTERY_MOTOR+_IN: Q4.D, Q5.D, Q6.D, U11.2 (VDD), U12.4 (COL); also elsewhere on the board
BATTERY_MOTOR+_OUT: J43.P$1, R13.2, R18.2, U8.3 (VIN+); also elsewhere on the board
BATTERY_MOTOR+_OUT_PRE: J42.P$1, Q4.S, Q5.S, Q6.S, R13.1, R16.2, U8.4 (VIN-)
GND: C23.1, C26.1, J51.P$1, R15.1, S3.1 (3), U8.2 (GND), U12.2 (CATH), U13.3 (GND); also elsewhere on the board
GND3: D1.C, D2.C (A), J63.P$1, R17.1, R20.1, U11.4 (GND); also elsewhere on the board
IMOTOR_A2D: J54.P$1, J59.P$1, R15.2, U8.1 (OUT)
unnamed: Q4.G, Q5.G, Q6.G, U11.5 (OUT)
unnamed: D1.A, D2.A (C), R18.1
unnamed: R22.1, U12.1 (A), U13.4 (O)
unnamed: S3.2 (1), U13.1 (I0)
unnamed: J97.P$1, R21.1, U13.2 (I1)
unnamed: R20.2, U11.3 (IN), U12.3 (E)
VMOTOR_A2D: J62.P$1, R16.1, R17.2

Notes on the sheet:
Reverse Polarity Protection with Enable Switch
Notes:
Motor Power Interface
When voltage input is: 32.764 V then Voltage output is: 3.302 V.

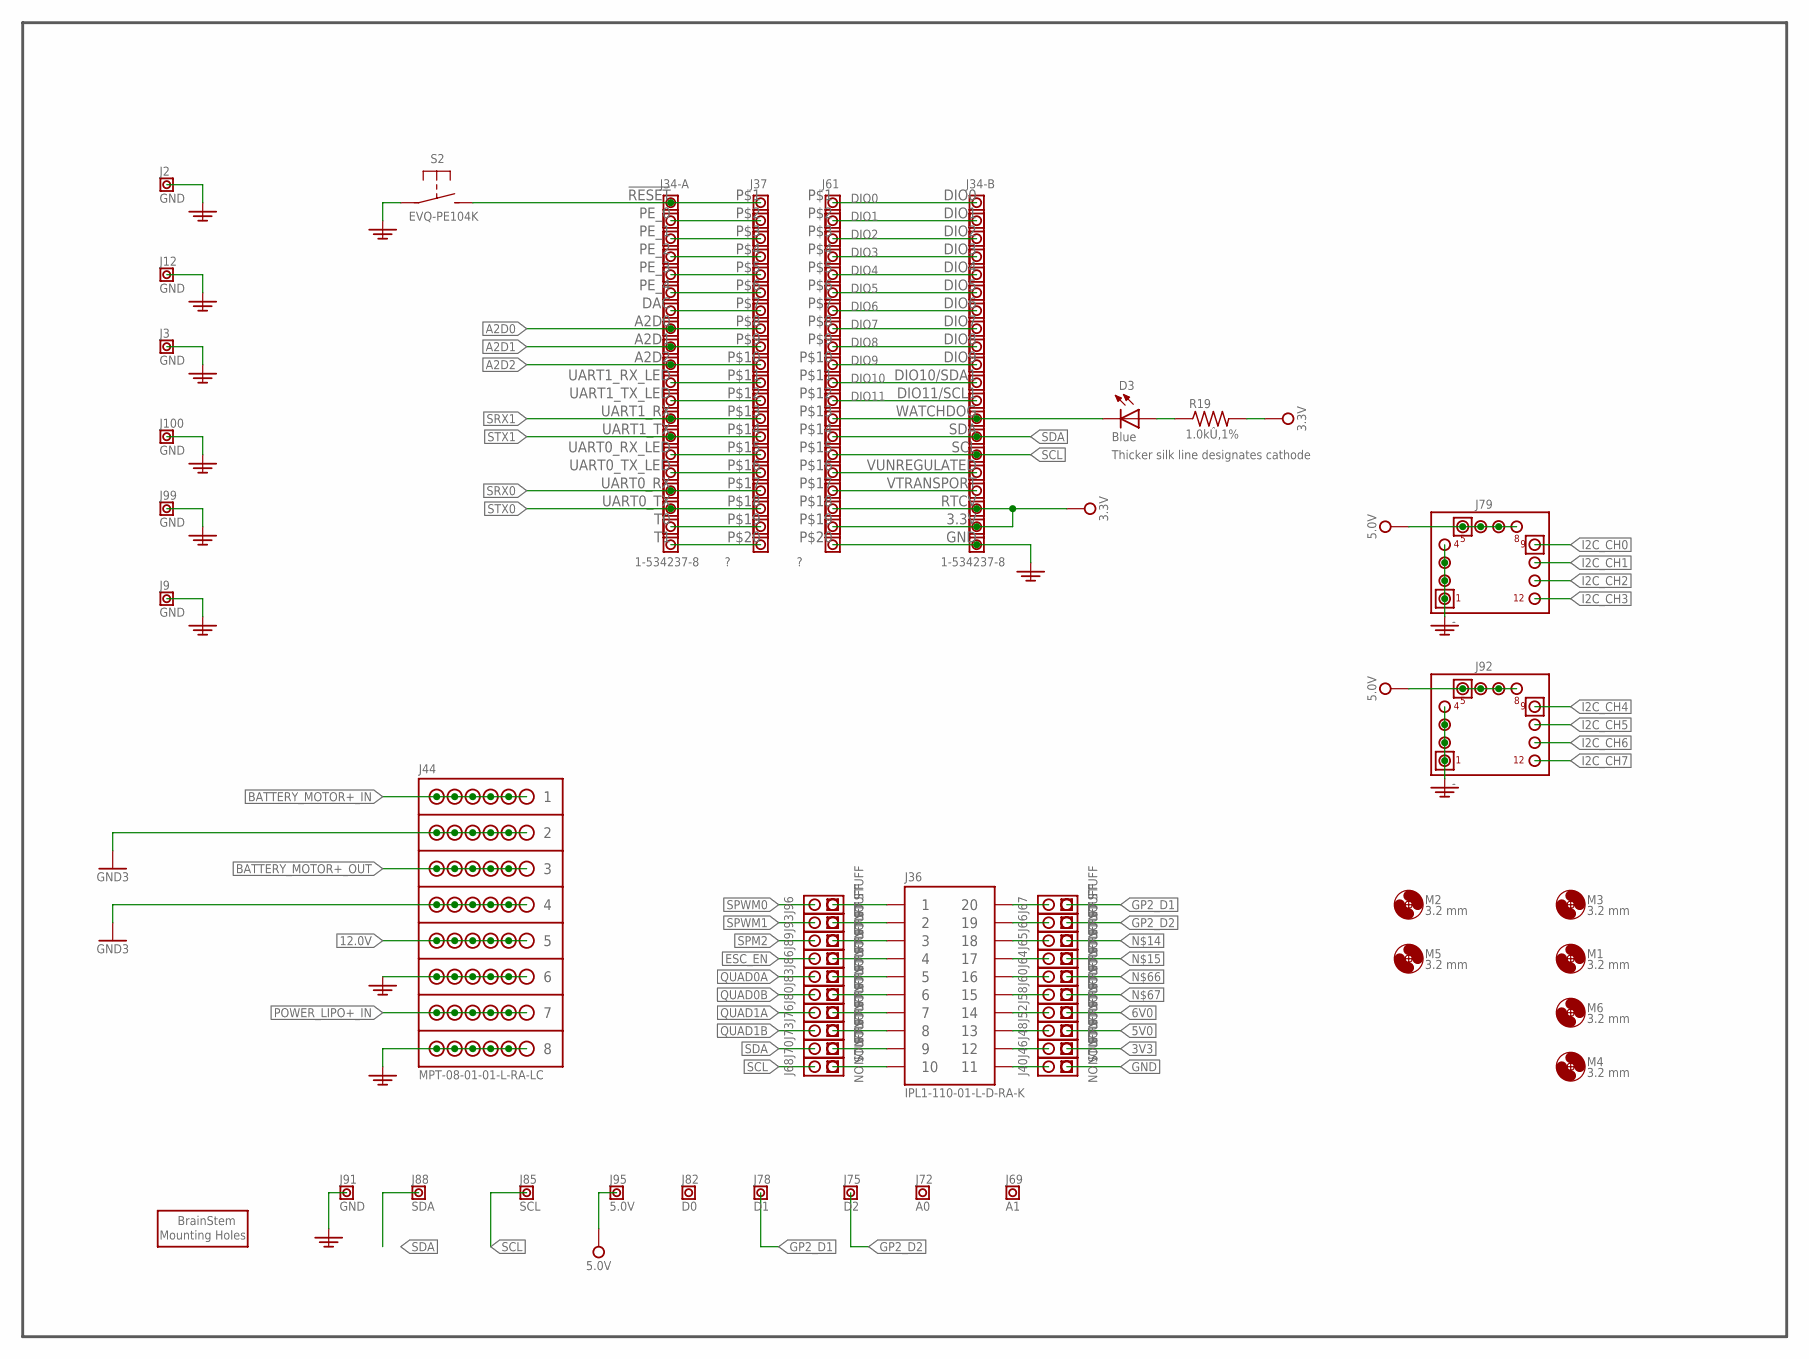
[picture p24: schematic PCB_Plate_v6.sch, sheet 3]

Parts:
D3: LTST-C171TBKT; CHIPLED_0805
J2, J3, J9, J12, J91, J99, J100: GND; TSW1X1_VAL
J34: BRAINSTEMSOCKET_FEMALE; BRAINSTEMSOCKET; PARTNUM 1-534237-8
J36: IPL1-1XX-02-XXX-DH-K-XX-MKT; IPL1-110-01-S-RA
J37, J61: TSW1X20
J40, J46, J48, J52, J58, J60, J64, J65, J66, J67, J68, J70, J73, J76, J80, J83, J86, J89, J93, J96: BOARD00012; TSW1X2
J44: MPT-08-01-01-L-RA-LC; MPT-08-XX-X-RA-XX
J69: A1; TSW1X1_VAL
J72: A0; TSW1X1_VAL
J75: D2; TSW1X1_VAL
J78: D1; TSW1X1_VAL
J79, J92: PCONN00012; TSW3X4RA
J82: D0; TSW1X1_VAL
J85: SCL; TSW1X1_VAL
J88: SDA; TSW1X1_VAL
J95: 5.0V; TSW1X1_VAL
M1, M2, M3, M4, M5, M6: MOUNT-HOLE3.2; 3,2
M7: BRAINSTEM_MOUNT
R19: PRESI00006; R0603
S2: EVQ-PE104K; SPST-NO

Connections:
3V3: J34.3.3V, J34.RTCV, J46.P$1, J61.P$18, J61.P$19, R19.2; also elsewhere on the board
5V0: J48.P$1, J79.P$5, J79.P$6, J79.P$7, J79.P$8, J92.P$5, J92.P$6, J92.P$7, J92.P$8, J95.P$1; also elsewhere on the board
6V0: J52.P$1
12.0V: J44.5@0 (5), J44.5@1 (5), J44.5@2 (5), J44.5@3 (5), J44.5@4 (5), J44.5@5 (5); also elsewhere on the board
!RESET: J34.!RESET, J37.P$1, S2.P$2 (S)
A2D0: J34.A2D0, J37.P$8; also elsewhere on the board
A2D1: J34.A2D1, J37.P$9; also elsewhere on the board
A2D2: J34.A2D2, J37.P$10; also elsewhere on the board
BATTERY_MOTOR+_IN: J44.1@0 (1), J44.1@1 (1), J44.1@2 (1), J44.1@3 (1), J44.1@4 (1), J44.1@5 (1); also elsewhere on the board
BATTERY_MOTOR+_OUT: J44.3@0 (3), J44.3@1 (3), J44.3@2 (3), J44.3@3 (3), J44.3@4 (3), J44.3@5 (3); also elsewhere on the board
DIO0: J34.DIO0, J61.P$1
DIO1: J34.DIO1, J61.P$2
DIO2: J34.DIO2, J61.P$3
DIO3: J34.DIO3, J61.P$4
DIO4: J34.DIO4, J61.P$5
DIO5: J34.DIO5, J61.P$6
DIO6: J34.DIO6, J61.P$7
DIO7: J34.DIO7, J61.P$8
DIO8: J34.DIO8, J61.P$9
DIO9: J34.DIO9, J61.P$10
DIO10: J34.DIO10/SDA1, J61.P$11
DIO11: J34.DIO11/SCL1, J61.P$12
ESC_EN: J86.P$2
GND: J2.P$1, J3.P$1, J9.P$1, J12.P$1, J34.GND, J40.P$1, J44.6@0 (6), J44.6@1 (6), J44.6@2 (6), J44.6@3 (6), J44.6@4 (6), J44.6@5 (6), J44.8@0 (1), J44.8@1 (1), J44.8@2 (1), J44.8@3 (1), J44.8@4 (1), J44.8@5 (8), J61.P$20, J79.P$1, J79.P$2, J79.P$3, J79.P$4, J91.P$1, J92.P$1, J92.P$2, J92.P$3, J92.P$4, J99.P$1, J100.P$1, S2.P$1; also elsewhere on the board
GND3: J44.2@0 (2), J44.2@1 (2), J44.2@2 (2), J44.2@3 (2), J44.2@4 (2), J44.2@5 (2), J44.4@0 (4), J44.4@1 (4), J44.4@2 (4), J44.4@3 (4), J44.4@4 (4), J44.4@5 (4); also elsewhere on the board
GP2_D1: J67.P$1, J78.P$1
GP2_D2: J66.P$1, J75.P$1
I2C_CH0: J79.P$9; also elsewhere on the board
I2C_CH1: J79.P$10; also elsewhere on the board
I2C_CH2: J79.P$11; also elsewhere on the board
I2C_CH3: J79.P$12; also elsewhere on the board
I2C_CH4: J92.P$9; also elsewhere on the board
I2C_CH5: J92.P$10; also elsewhere on the board
I2C_CH6: J92.P$11; also elsewhere on the board
I2C_CH7: J92.P$12; also elsewhere on the board
unnamed: D3.A, R19.1
unnamed: D3.C, J34.WATCHDOG, J61.P$13
unnamed: J34.PE_0, J37.P$2
unnamed: J34.PE_1, J37.P$3
unnamed: J34.PE_2, J37.P$4
unnamed: J34.PE_3, J37.P$5
unnamed: J34.PE_4, J37.P$6
unnamed: J34.DAC, J37.P$7
unnamed: J34.UART1_RX_LED, J37.P$11
unnamed: J34.UART1_TX_LED, J37.P$12
unnamed: J34.UART0_RX_LED, J37.P$15
unnamed: J34.UART0_TX_LED, J37.P$16
unnamed: J34.T0, J37.P$19
unnamed: J34.T1, J37.P$20
unnamed: J34.VTRANSPORT, J61.P$17
unnamed: J36.1, J96.P$1
unnamed: J36.2, J93.P$1
unnamed: J36.3, J89.P$1
unnamed: J36.4, J86.P$1
unnamed: J36.5, J83.P$1
unnamed: J36.6, J80.P$1
unnamed: J36.7, J76.P$1
unnamed: J36.8, J73.P$1
unnamed: J36.9, J70.P$1
unnamed: J36.10, J68.P$1
unnamed: J36.20, J67.P$2
unnamed: J36.19, J66.P$2
unnamed: J36.18, J65.P$2
unnamed: J36.17, J64.P$2
unnamed: J36.16, J60.P$2
unnamed: J36.15, J58.P$2
unnamed: J36.14, J52.P$2
unnamed: J36.13, J48.P$2
unnamed: J36.12, J46.P$2
unnamed: J36.11, J40.P$2
unnamed: J34.VUNREGULATED, J61.P$16
POWER_LIPO+_IN: J44.7@0 (7), J44.7@1 (7), J44.7@2 (7), J44.7@3 (7), J44.7@4 (7), J44.7@5 (7); also elsewhere on the board
QUAD0A: J83.P$2
QUAD0B: J80.P$2
QUAD1A: J76.P$2
QUAD1B: J73.P$2
SCL: J34.SCL, J61.P$15, J68.P$2, J85.P$1; also elsewhere on the board
SDA: J34.SDA, J61.P$14, J70.P$2, J88.P$1; also elsewhere on the board
SPM2: J89.P$2
SPWM0: J96.P$2
SPWM1: J93.P$2
SRX0: J34.UART0_RX, J37.P$17; also elsewhere on the board
SRX1: J34.UART1_RX, J37.P$13; also elsewhere on the board
STX0: J34.UART0_TX, J37.P$18; also elsewhere on the board
STX1: J34.UART1_TX, J37.P$14; also elsewhere on the board

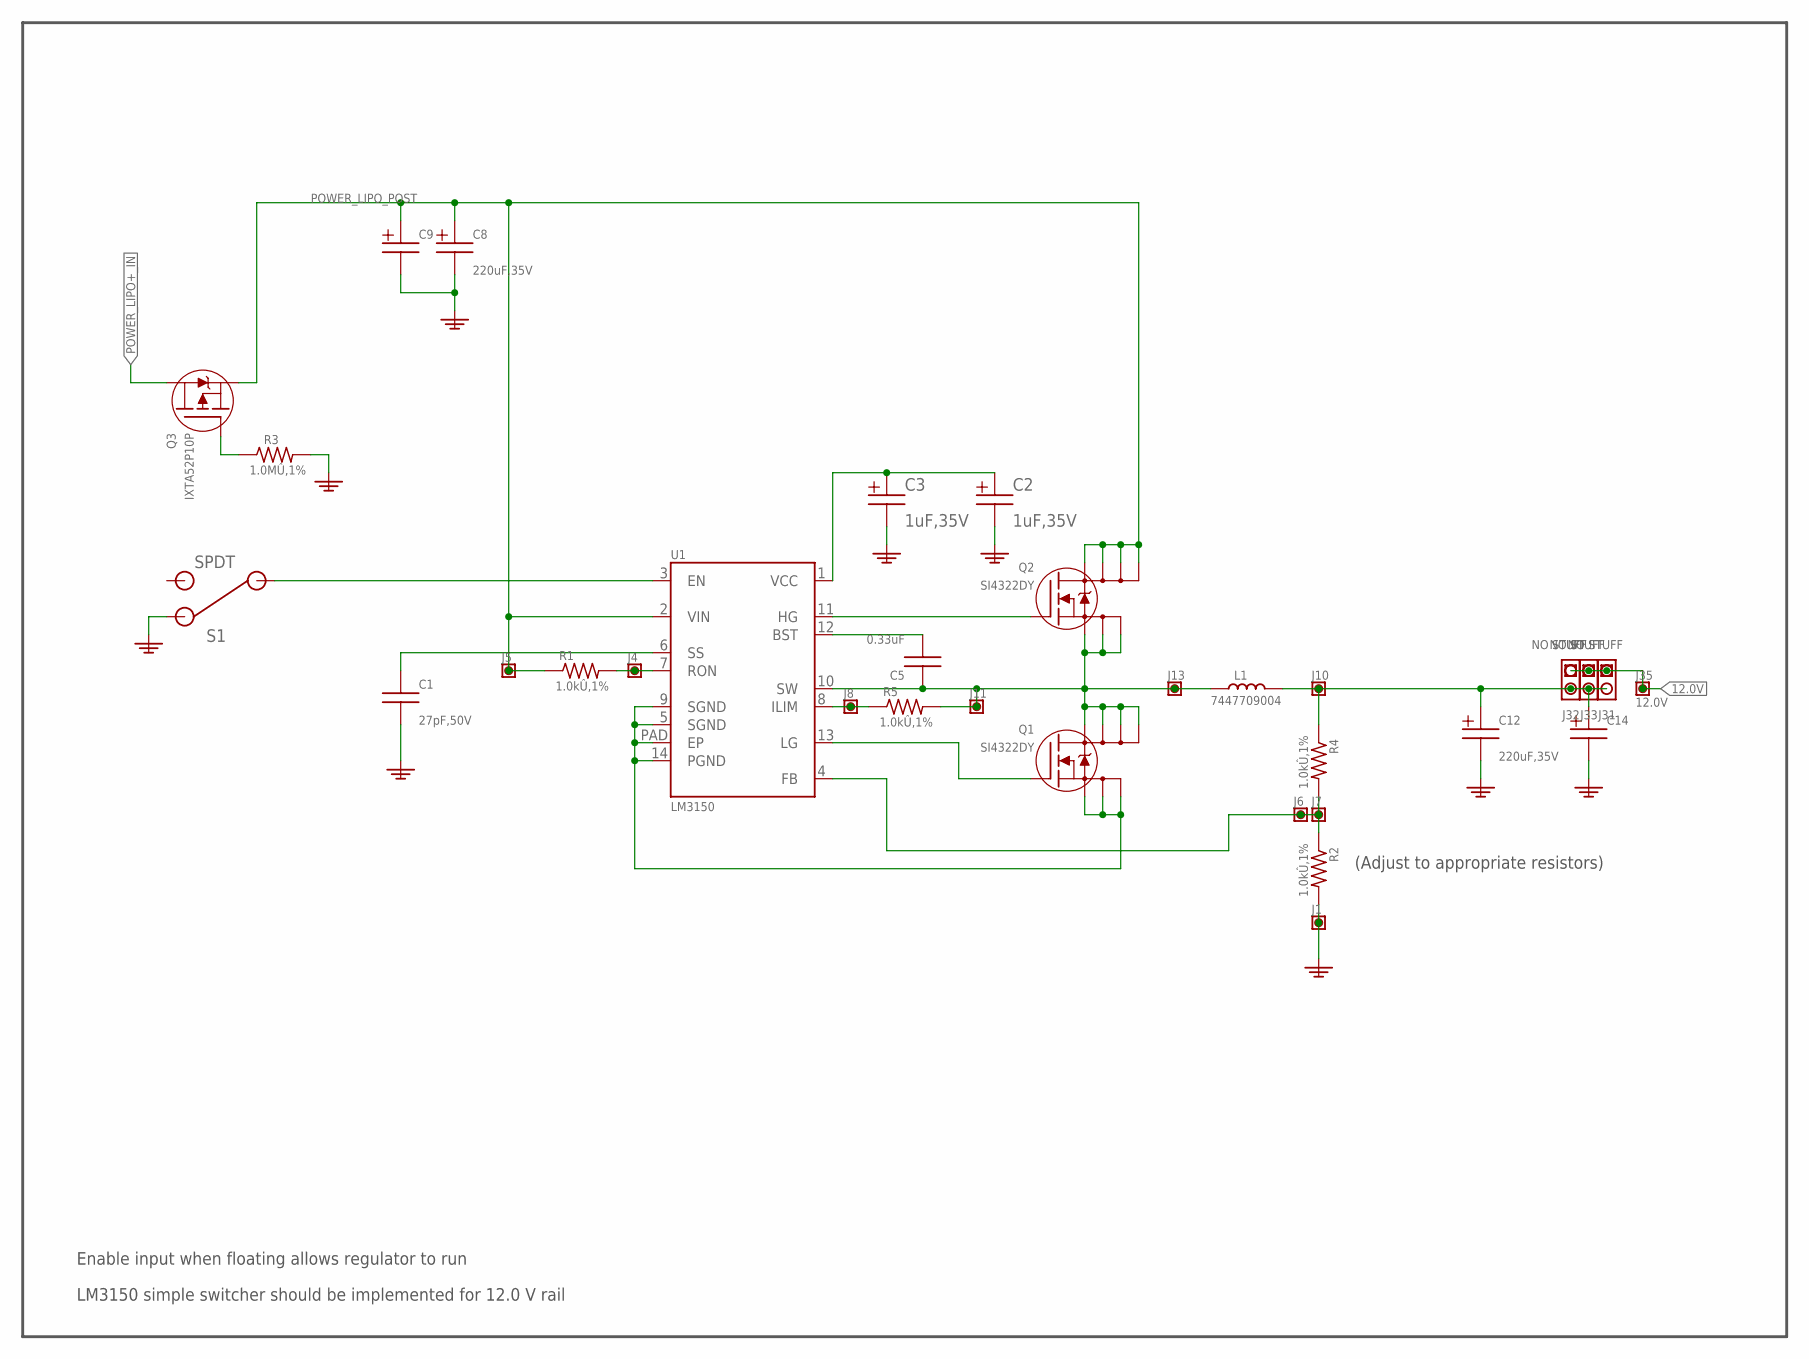
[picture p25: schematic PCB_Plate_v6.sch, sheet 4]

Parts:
C1: ECJ-1VC1H270J; C0603
C2, C3: T491B105K035AT; T491
C5: PCAPI00005; C0603
C8, C12: PCAPI00020; PANASONIC_G
C9, C14: CAP_POLARIZED; PANASONIC_NHG_A
J1, J4, J5, J6, J7, J8, J10, J11, J13: BOARD00003; TSW1X1
J31, J32, J33: BOARD00012; TSW1X2
J35: 12.0V; TSW1X1_VAL
L1: 7447709004
Q1, Q2: SI4322DY; SO-08
Q3: IXTA52P10P; D2PACK
R1, R2, R4, R5: PRESI00006; R0603
R3: ERJ-3EKF1004V; R0603
S1: PMISC00005; SPDTRA
U1: LM3150; TSSOP14EXP

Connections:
12.0V: J31.P$1, J32.P$1, J33.P$1, J35.P$1; also elsewhere on the board
GND: C1.2, C2.-, C3.-, C8.-, C9.-, C12.-, C14.-, J1.P$1, R2.2, R3.2, S1.1 (3); also elsewhere on the board
unnamed: S1.2 (1), U1.3 (EN)
unnamed: C12.+, C14.+, J10.P$1, J31.P$2, J32.P$2, J33.P$2, L1.2, R4.1
unnamed: C2.+, C3.+, U1.1 (VCC)
unnamed: Q1.1 (SA), Q1.2 (SB), Q1.3 (SC), U1.5 (SGND), U1.9 (SGND), U1.14 (PGND), U1.PAD (EP)
unnamed: Q1.4 (G), U1.13 (LG)
unnamed: Q2.4 (G), U1.11 (HG)
unnamed: Q3.G, R3.1
unnamed: J4.P$1, R1.2, U1.7 (RON)
unnamed: C5.1, J11.P$1, J13.P$1, L1.1, Q1.5 (DA), Q1.6 (DB), Q1.7 (DC), Q1.8 (DD), Q2.1 (SA), Q2.2 (SB), Q2.3 (SC), R5.2, U1.10 (SW)
unnamed: C5.2, U1.12 (BST)
unnamed: J6.P$1, J7.P$1, R2.1, R4.2, U1.4 (FB)
unnamed: J8.P$1, R5.1, U1.8 (ILIM)
unnamed: C1.1, U1.6 (SS)
POWER_LIPO+_IN: Q3.D; also elsewhere on the board
POWER_LIPO_POST: C8.+, C9.+, J5.P$1, Q2.5 (DA), Q2.6 (DB), Q2.7 (DC), Q2.8 (DD), Q3.S, R1.1, U1.2 (VIN)

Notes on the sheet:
LM3150 simple switcher should be implemented for 12.0 V rail
Enable input when floating allows regulator to run
(Adjust to appropriate resistors)

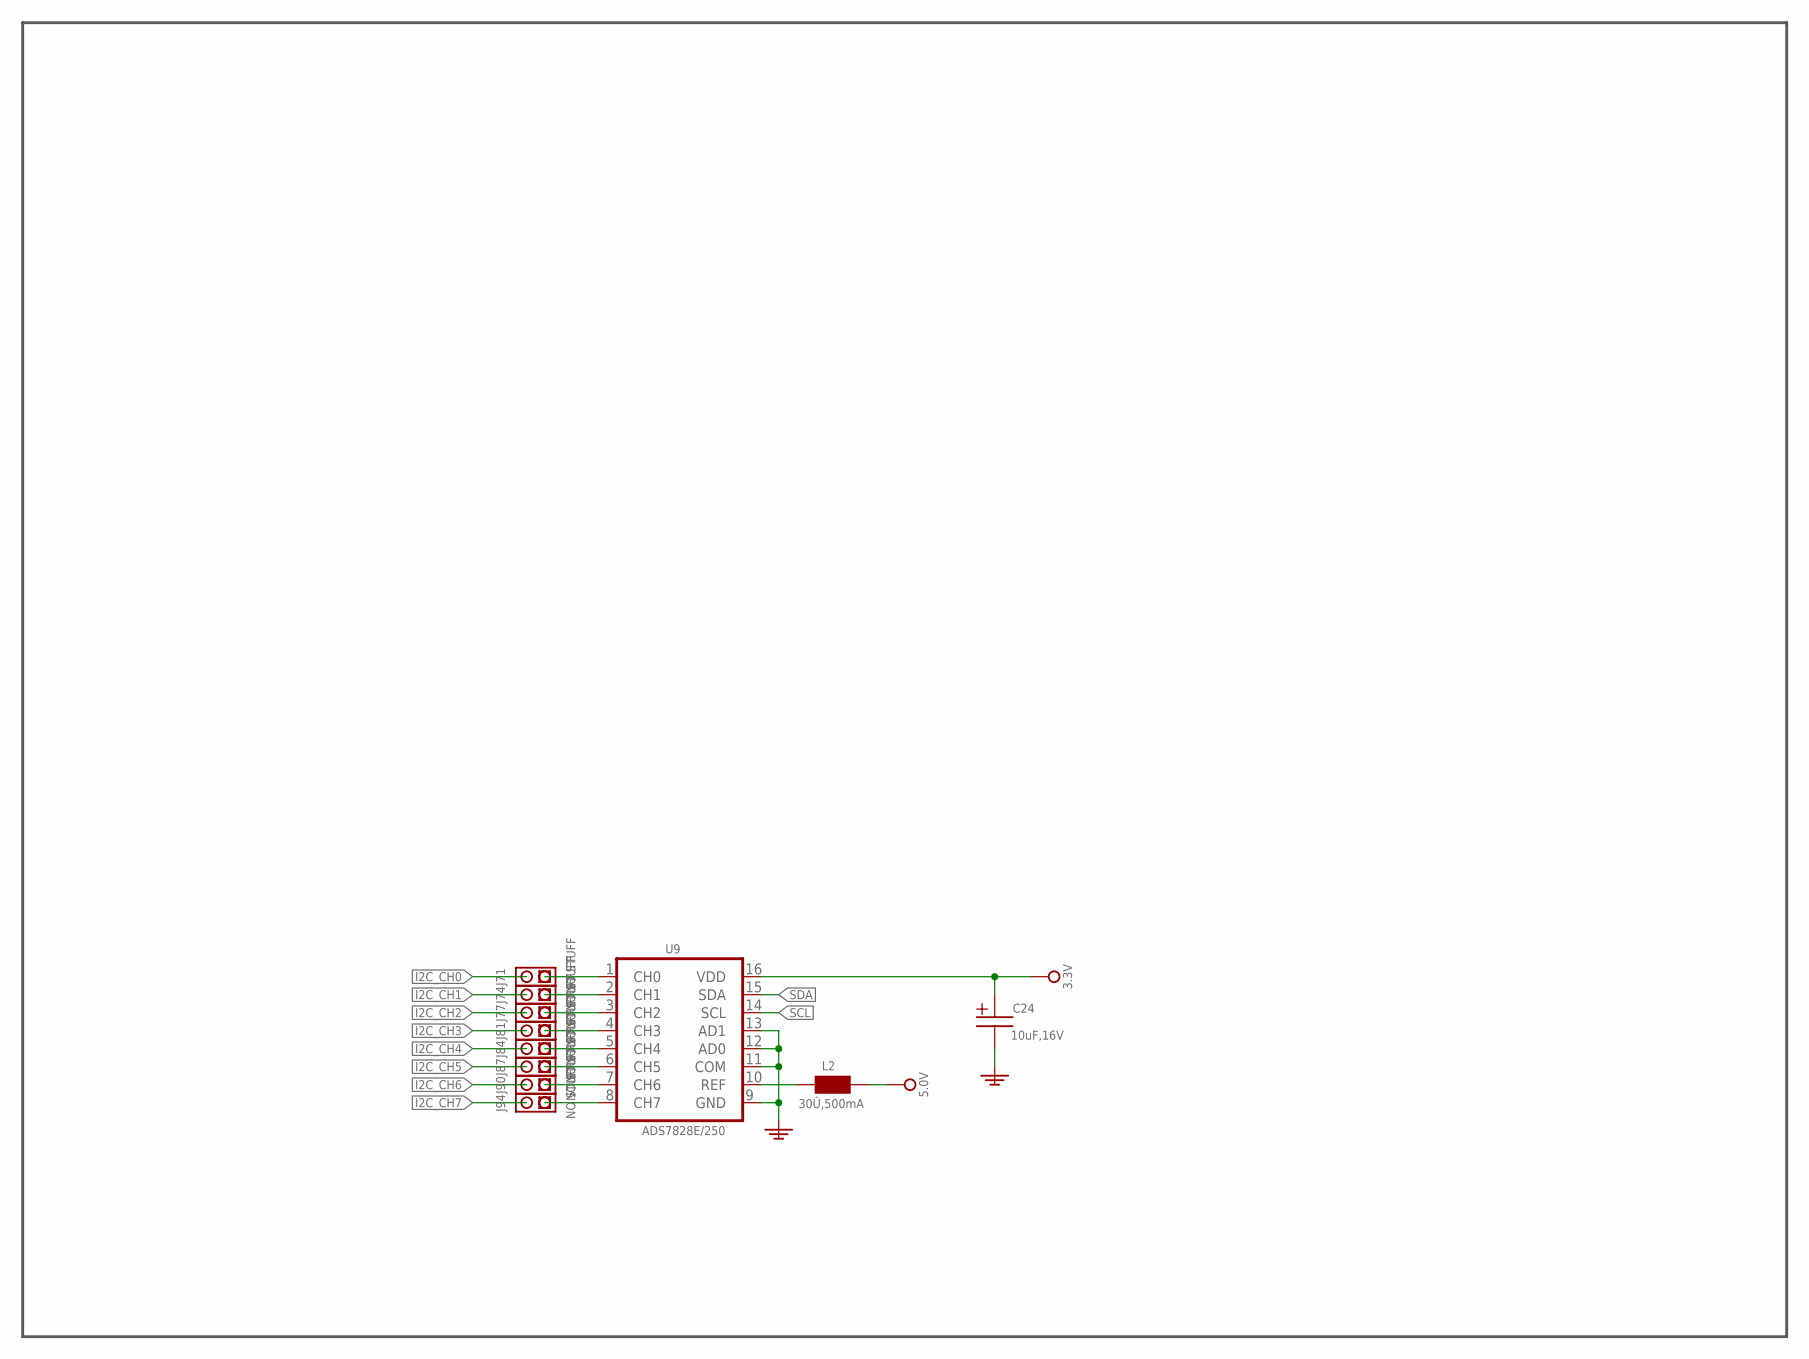
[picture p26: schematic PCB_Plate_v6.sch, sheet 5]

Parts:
C24: T491A106K010AT; SMC_A
J71, J74, J77, J81, J84, J87, J90, J94: BOARD00012; TSW1X2
L2: PMISC00013; L0402
U9: ADS7828E; TSSOP16

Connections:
3V3: C24.+, U9.16 (VDD); also elsewhere on the board
5V0: L2.2; also elsewhere on the board
GND: C24.-, U9.9 (GND), U9.11 (COM), U9.12 (AD0), U9.13 (AD1); also elsewhere on the board
I2C_CH0: J71.P$2; also elsewhere on the board
I2C_CH1: J74.P$2; also elsewhere on the board
I2C_CH2: J77.P$2; also elsewhere on the board
I2C_CH3: J81.P$2; also elsewhere on the board
I2C_CH4: J84.P$2; also elsewhere on the board
I2C_CH5: J87.P$2; also elsewhere on the board
I2C_CH6: J90.P$2; also elsewhere on the board
I2C_CH7: J94.P$2; also elsewhere on the board
unnamed: J71.P$1, U9.1 (CH0)
unnamed: L2.1, U9.10 (REF)
unnamed: J74.P$1, U9.2 (CH1)
unnamed: J77.P$1, U9.3 (CH2)
unnamed: J81.P$1, U9.4 (CH3)
unnamed: J84.P$1, U9.5 (CH4)
unnamed: J87.P$1, U9.6 (CH5)
unnamed: J90.P$1, U9.7 (CH6)
unnamed: J94.P$1, U9.8 (CH7)
SCL: U9.14 (SCL); also elsewhere on the board
SDA: U9.15 (SDA); also elsewhere on the board

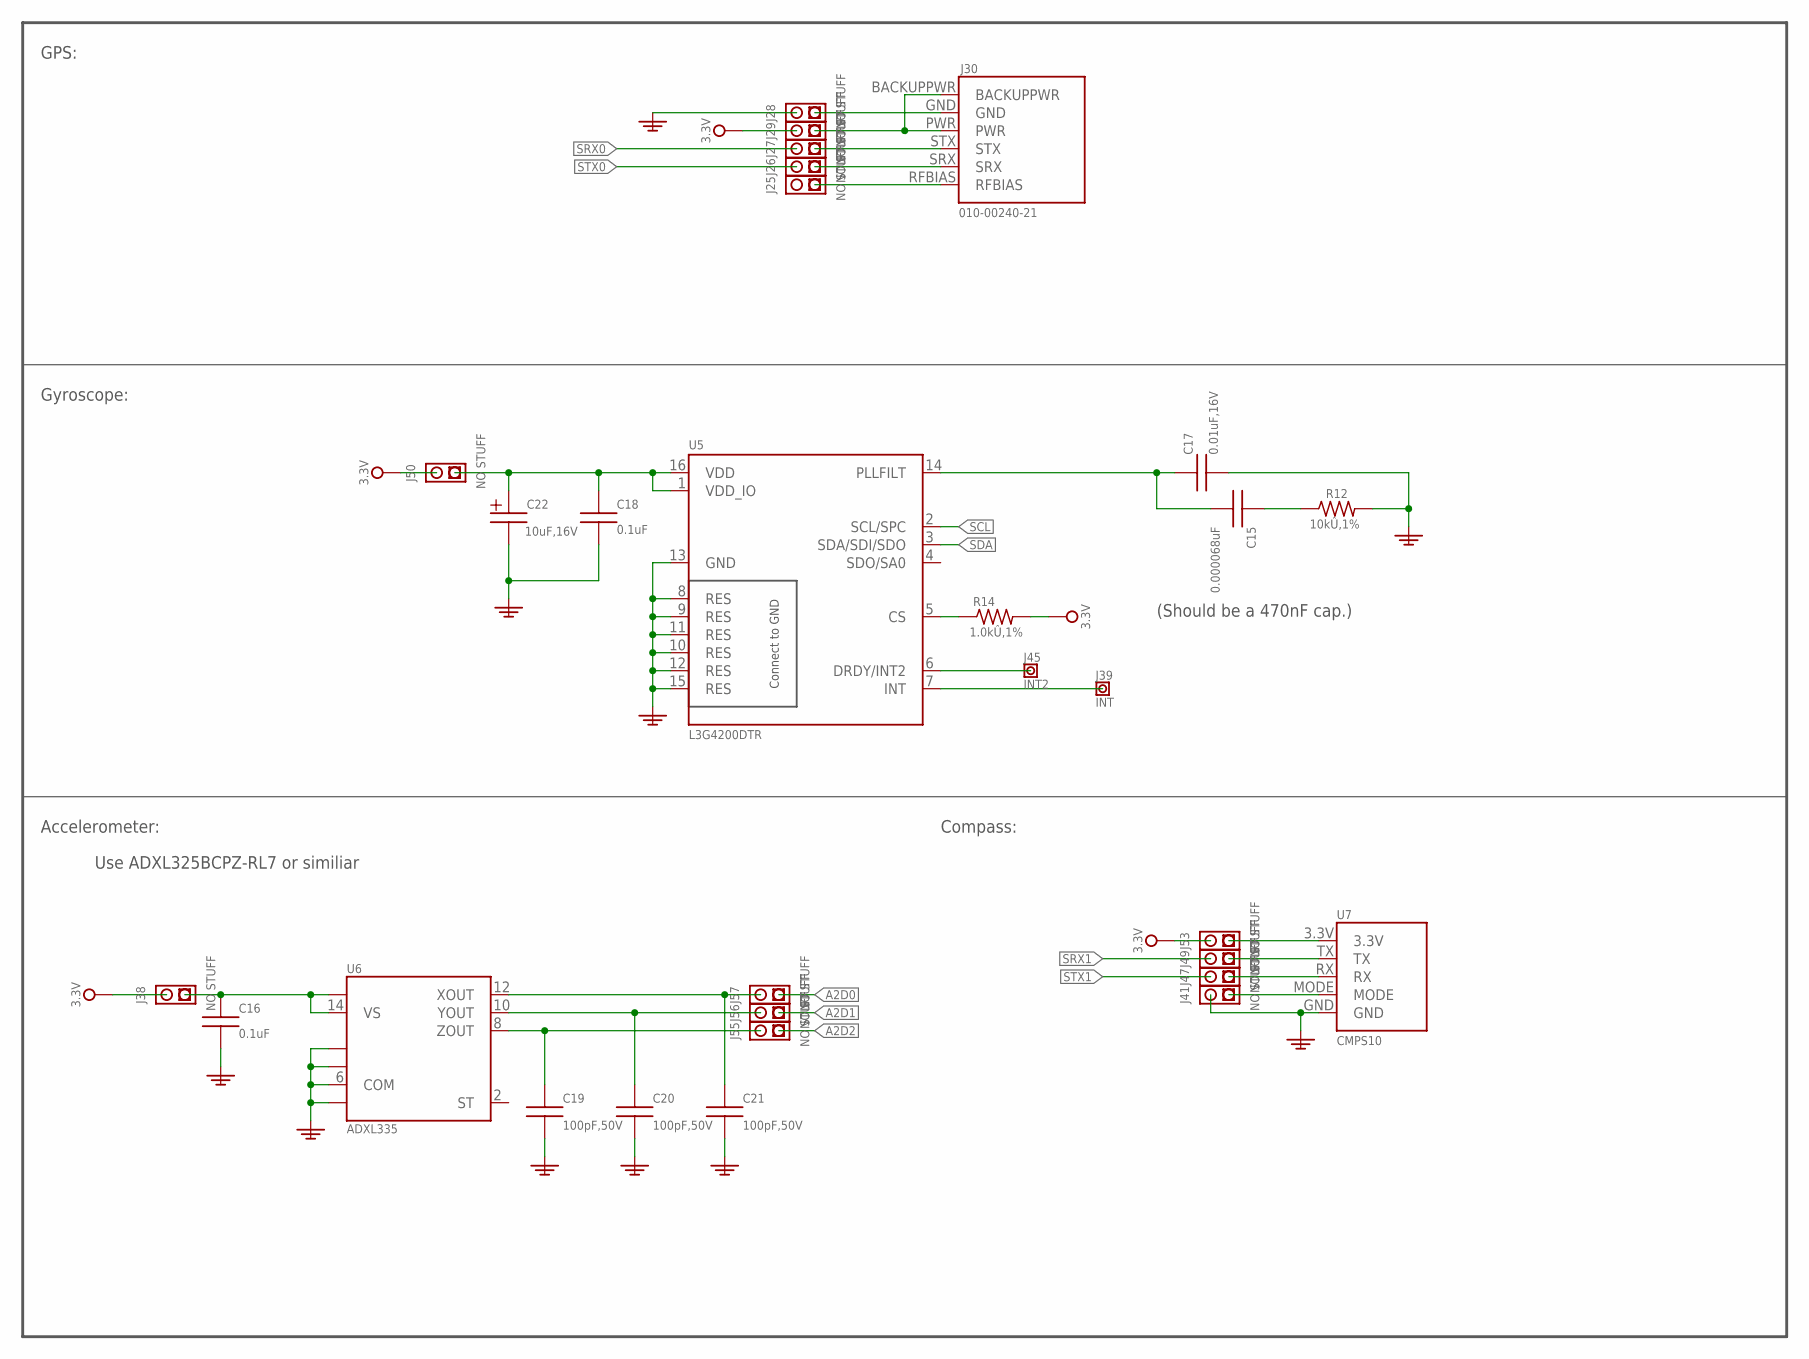
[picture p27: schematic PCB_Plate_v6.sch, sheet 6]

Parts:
C15: PCAPI00023; C0603
C16, C18: PCAPI00015; C0603
C17: PCAPI00007; C0603
C19, C20, C21: PCAPI00016; C0603
C22: T491A106K010AT; SMC_A
J25, J26, J27, J28, J29, J38, J41, J47, J49, J50, J53, J55, J56, J57: BOARD00012; TSW1X2
J30: GPS15X; GPS15
J39: INT; TSW1X1_VAL
J45: INT2; TSW1X1_VAL
R12: PRESI00005; R0603
R14: PRESI00006; R0603
U5: L3G4200DTR; LGA16
U6: ADXL335; LFCSP-16
U7: CMPS10

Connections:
3V3: J29.P$2, J38.P$2, J50.P$2, J53.P$2, R14.2; also elsewhere on the board
A2D0: J57.P$1; also elsewhere on the board
A2D1: J56.P$1; also elsewhere on the board
A2D2: J55.P$1; also elsewhere on the board
GND: C16.2, C17.2, C18.2, C19.2, C20.2, C21.2, C22.-, J28.P$2, J41.P$2, R12.2, U5.8 (RES), U5.9 (RES), U5.10 (RES), U5.11 (RES), U5.12 (RES), U5.13 (GND), U5.15 (RES), U6.3 (COM), U6.5 (COM), U6.6 (COM), U6.7 (COM), U7.GND; also elsewhere on the board
unnamed: J41.P$1, U7.MODE
unnamed: C18.1, C22.+, J50.P$1, U5.1 (VDD_IO), U5.16 (VDD)
unnamed: R14.1, U5.5 (CS)
unnamed: J29.P$1, J30.BACKUPPWR, J30.PWR
unnamed: J28.P$1, J30.GND
unnamed: J27.P$1, J30.STX
unnamed: J26.P$1, J30.SRX
unnamed: J25.P$1, J30.RFBIAS
unnamed: C15.2, C17.1, U5.14 (PLLFILT)
unnamed: C15.1, R12.1
unnamed: J39.P$1, U5.7 (INT)
unnamed: J45.P$1, U5.6 (DRDY/INT2)
unnamed: J53.P$1, U7.3.3V
unnamed: J49.P$1, U7.TX
unnamed: J47.P$1, U7.RX
unnamed: C16.1, J38.P$1, U6.14 (VS), U6.15 (VS)
unnamed: C19.1, J55.P$2, U6.8 (ZOUT)
unnamed: C20.1, J56.P$2, U6.10 (YOUT)
unnamed: C21.1, J57.P$2, U6.12 (XOUT)
SCL: U5.2 (SCL/SPC); also elsewhere on the board
SDA: U5.3 (SDA/SDI/SDO); also elsewhere on the board
SRX0: J27.P$2; also elsewhere on the board
SRX1: J49.P$2; also elsewhere on the board
STX0: J26.P$2; also elsewhere on the board
STX1: J47.P$2; also elsewhere on the board

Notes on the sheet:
Gyroscope:
GPS:
Accelerometer:
(Should be a 470nF cap.)
Use ADXL325BCPZ-RL7 or similiar
Compass:

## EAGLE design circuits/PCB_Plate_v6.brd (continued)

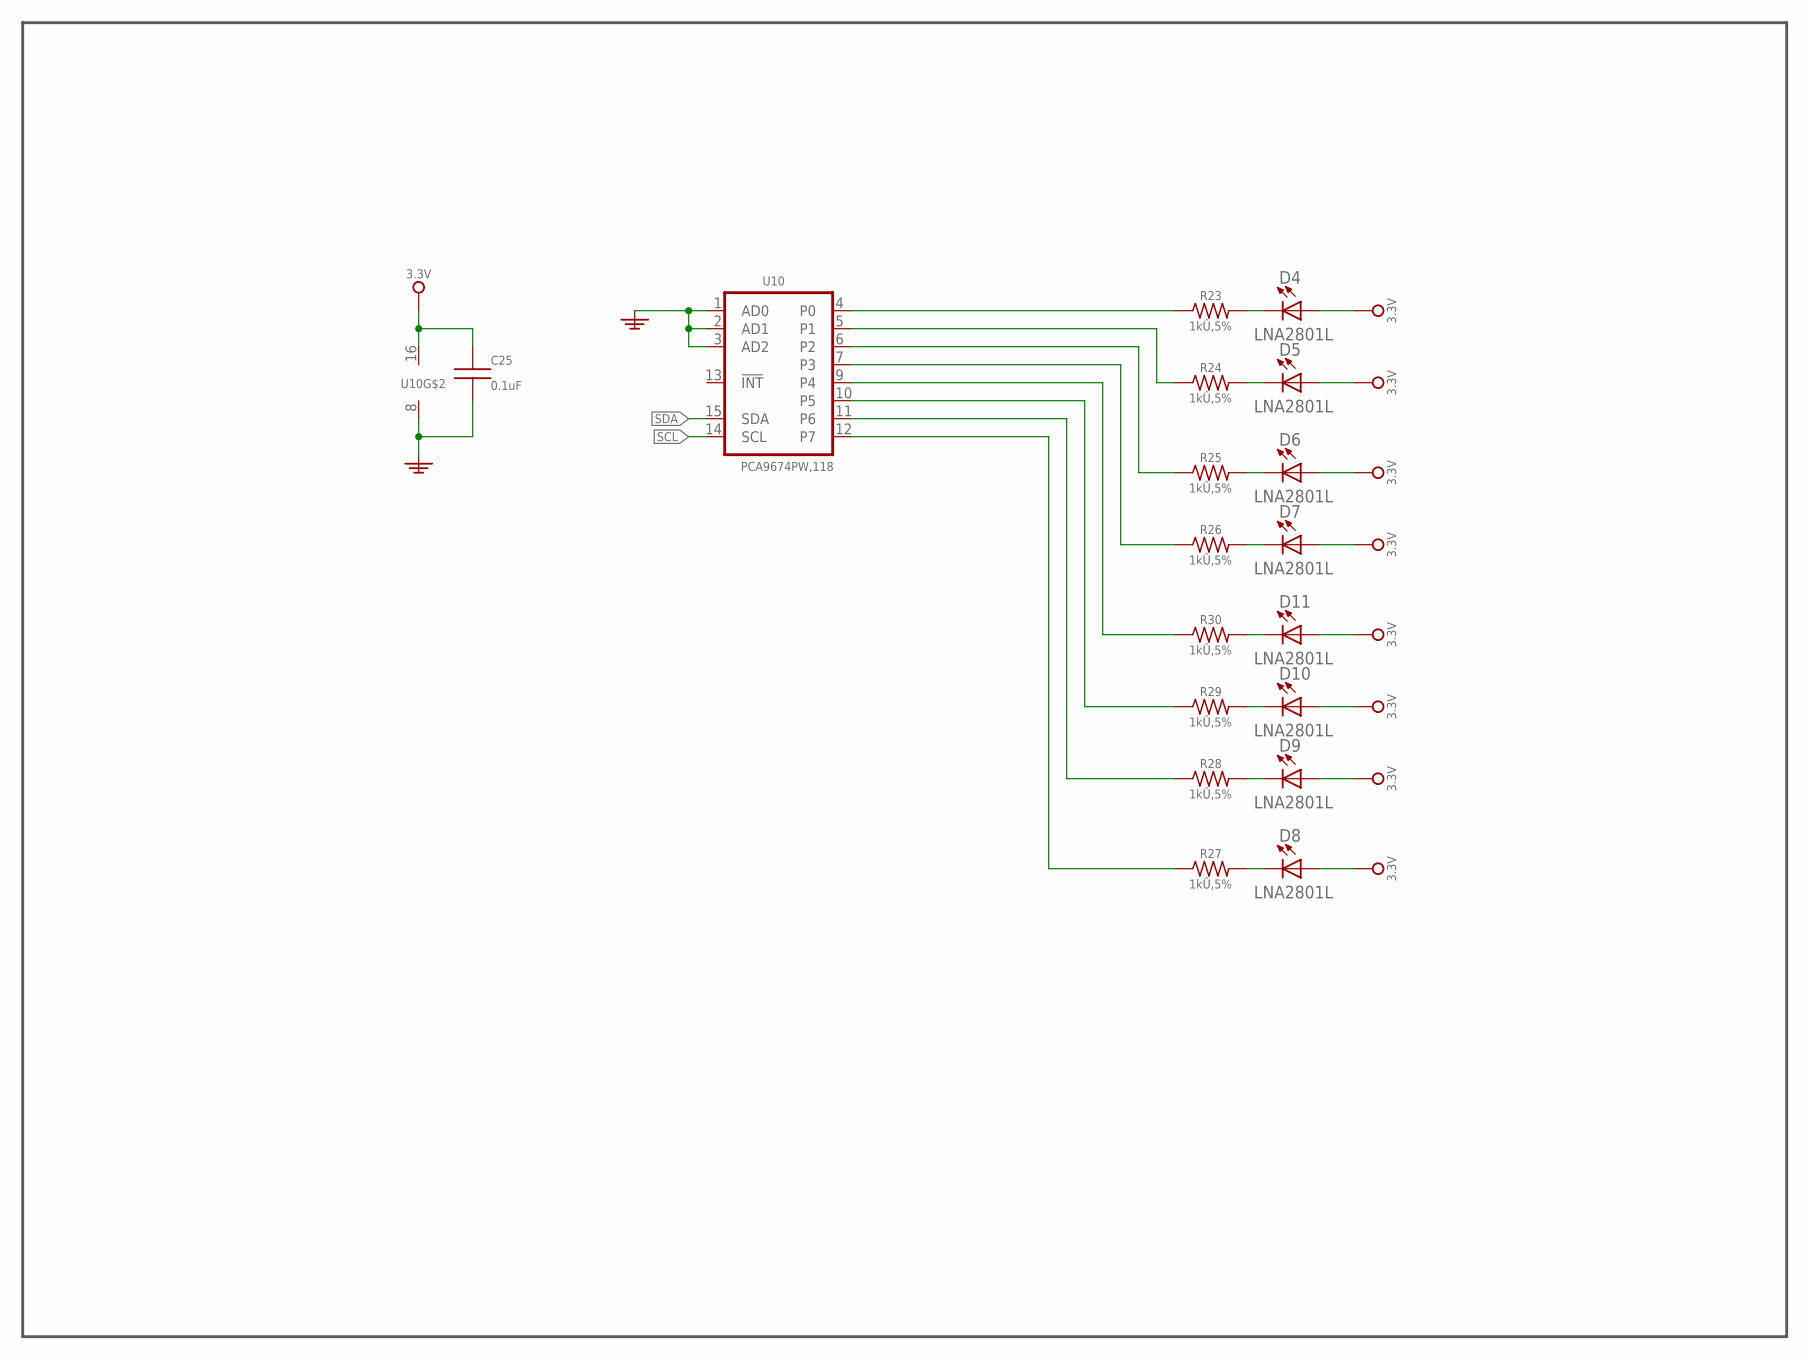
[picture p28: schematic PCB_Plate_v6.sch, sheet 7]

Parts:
C25: PCAPI00015; C0603
D4, D5, D6, D7, D8, D9, D10, D11: PDIOD00003; LT3LR1N02-001
R23, R24, R25, R26, R27, R28, R29, R30: PRESI00012; CFR-12
U10: I2C_DIO_EXPANDER; TSSOP16

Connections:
3V3: C25.1, D4.A, D5.A, D6.A, D7.A, D8.A, D9.A, D10.A, D11.A, U10.16 (VCC); also elsewhere on the board
GND: C25.2, U10.1 (AD0), U10.2 (AD1), U10.3 (AD2), U10.8 (GND); also elsewhere on the board
unnamed: D4.C, R23.P$2 (2)
unnamed: R23.P$1 (1), U10.4 (P0)
unnamed: D5.C, R24.P$2 (2)
unnamed: D6.C, R25.P$2 (2)
unnamed: D7.C, R26.P$2 (2)
unnamed: D11.C, R30.P$2 (2)
unnamed: D10.C, R29.P$2 (2)
unnamed: D9.C, R28.P$2 (2)
unnamed: D8.C, R27.P$2 (2)
unnamed: R24.P$1 (1), U10.5 (P1)
unnamed: R25.P$1 (1), U10.6 (P2)
unnamed: R26.P$1 (1), U10.7 (P3)
unnamed: R30.P$1 (1), U10.9 (P4)
unnamed: R29.P$1 (1), U10.10 (P5)
unnamed: R28.P$1 (1), U10.11 (P6)
unnamed: R27.P$1 (1), U10.12 (P7)
SCL: U10.14 (SCL); also elsewhere on the board
SDA: U10.15 (SDA); also elsewhere on the board

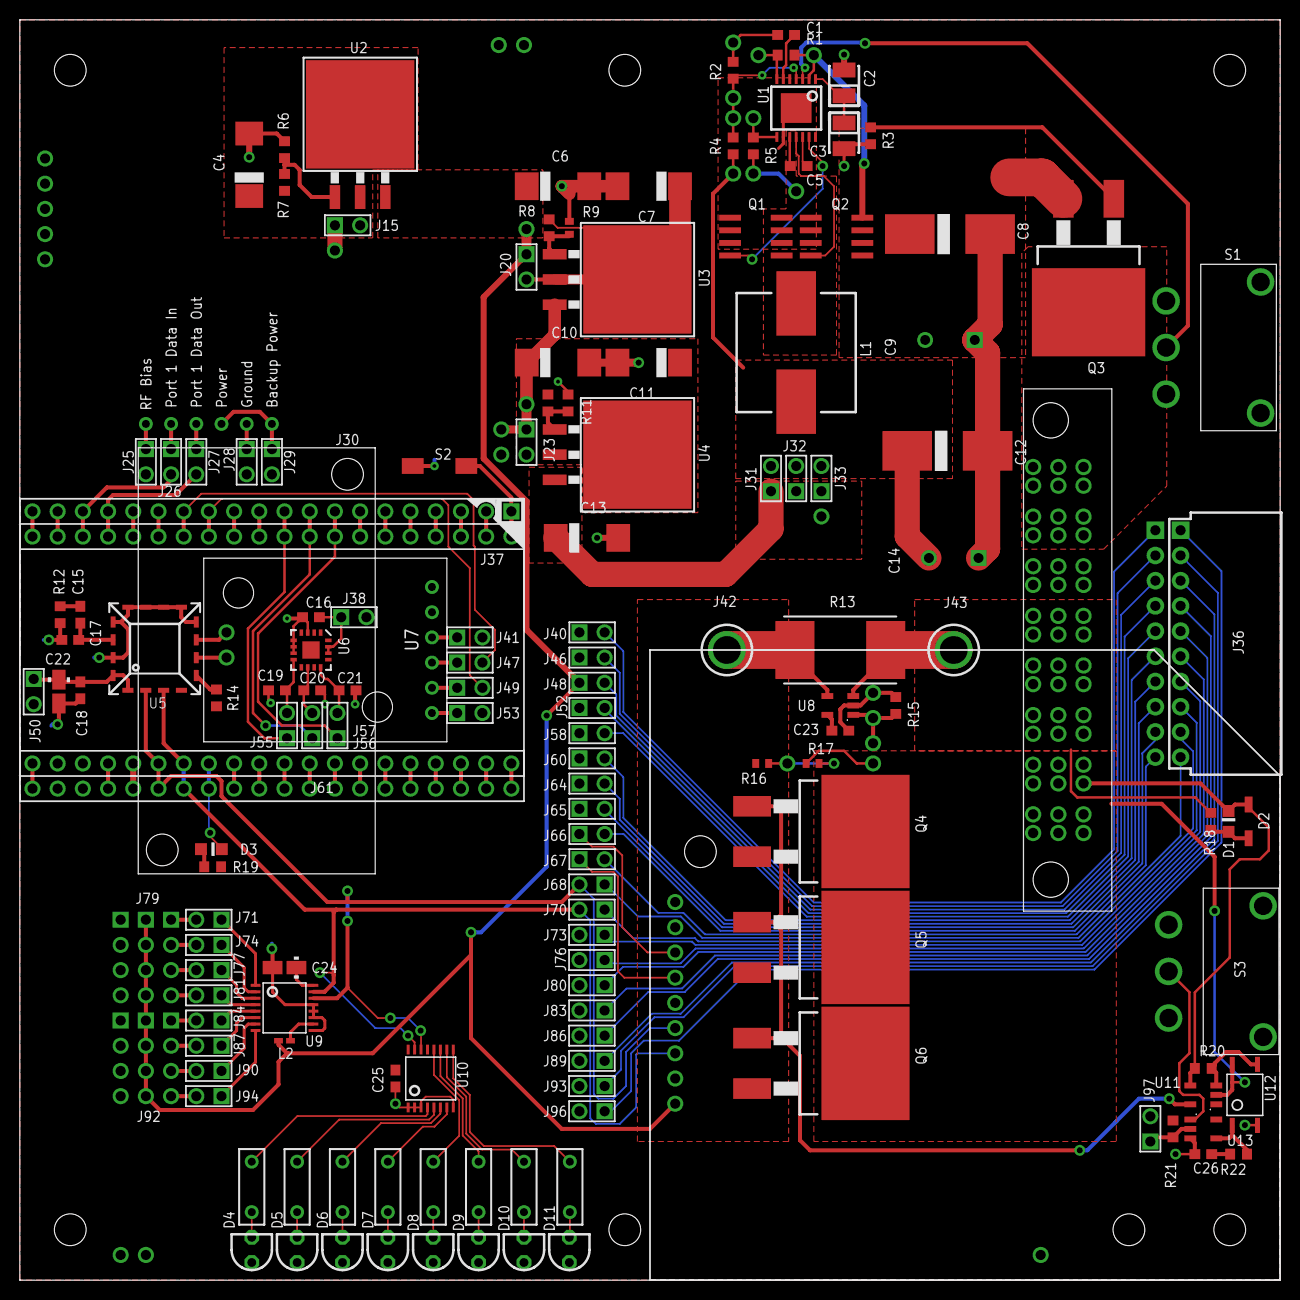
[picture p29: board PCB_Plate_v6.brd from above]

Board: 2 copper layers, 127.0 x 127.0 mm, 198 parts (0 on the bottom side), 150 nets.

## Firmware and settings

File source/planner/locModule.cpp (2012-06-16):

#include "locModule.h"
#include <sys/time.h>

//We'll wait up to 30 seconds for a GPS lock on initialization.
#define aGPS_LOCK_STEPS 3
#define DEG_TO_RAD (aPI/180)
#define RAD_TO_DEG (180/aPI)
////////////////////////////////////////////////////////////////////////////
aErr
avcPosition::init(acpStem* pStem, 
                  aSettingFileRef settings, 
                  avcWaypointVector firstMapPoint) {


  aErr e = aErrNone;

  m_pStem = pStem;
  m_settings = settings;
  m_logger = logger::getInstance();

  m_pCompass = new LSM303DLM(m_pStem, m_settings);
  m_pCompass->init();

  // make an accelerometer class and start a thread for the EKF
  //m_pAccel = new accelerometerADXL335(m_pStem, m_settings);
  //m_pAccel->init();
  //m_pAccelThread = new avcAccelerometerThread(m_pAccel);


	
  //first we'll grab some settings from the settings file.
  float fSetVar;

  if(aSettingFile_GetFloat(m_ioRef, m_settings, KEY_METER_PER_TICK,
                           &fSetVar, METER_PER_TICK, &e))
    throw acpException(e, "getting meter per tick");
    m_metersPerTick = fSetVar;
  
  if(aSettingFile_GetFloat(m_ioRef, m_settings, aKEY_WHEEL_BASE,  
                           &fSetVar, WHEEL_BASE, &e))
    throw acpException(e, "getting wheel track from settings");
  m_wheelBase = fSetVar;
	
	if(aSettingFile_GetFloat(m_ioRef, m_settings, "gpsdead_scaling_heading",
                           &m_fScalingErrorHeading, 1.0f, &e))
    throw acpException(e, "getting heading scaling constant");
  
	if(aSettingFile_GetFloat(m_ioRef, m_settings, "gpsdead_scaling_position",
                           &m_fScalingErrorPosition, 1.0f, &e))
    throw acpException(e, "getting position scaling constant");
	
  // Set the first position waypoint that we passed in
  setPosition(firstMapPoint);

  if (m_pStem && m_pStem->isConnected()) {
		
    //Lets initialize the encoders to zero.
    m_pStem->MO_ENC32(aMOTO_MODULE, ENCODER_IDX, 0);
    m_Encoder = 0;
    m_lastDistanceTraveled = 0.0;
		
#ifdef aUSE_GPS

    /*lets do some initialization. First we need to find out
    * whether we have a good GPS signal. If we do, we'll init
    * our starting position from the GPS position information
    * else we'll assume we're at the 0,0,0 position.
    */
    
    m_pGPS = gps::getInstance();
		
		aSettingFileRef gpsSettings;
		aSettingFile_Create(m_ioRef, "gps.config", &gpsSettings, &e);

    m_pGPS->init(gpsSettings);
    m_pGpsThread = acpOSFactory::thread("gps");
    m_pGpsThread->start(m_pGPS);

    int timeout = 0;
    bool haveGPS = false;
    while (timeout < aGPS_LOCK_STEPS) {
        m_logger->log(INFO, "Getting GPS Lock %d", timeout);
        int quality = m_pGPS->getQuality();
        if(quality) {
            m_logger->log(INFO, "Locked GPS: quality(%d)", quality);
            haveGPS = true;
            break;
        }
        aIO_MSSleep(m_ioRef, 2000, NULL);
        ++timeout;
    }

    if (haveGPS) {
        // Lets get a lat, lon, and heading. We shouldn't
        // be moving yet. We're also not going to get
        // a good heading from our GPS, so we use the
        // compass.
        float lon, lat, head;
        if(m_pGPS->getPosition(&lon, &lat, &head) == aErrNone) {

            // We want heading from the compass, but
            // we'll fall back on the gps heading if we can't
            // get it.
            m_pCompass->getHeadingDeg(&head);

            setPosition(avcWaypointVector(lon,
                                          lat,
                                          head));
        }
    }
    //else the default initilization of the state vector
    //and probability matrix is zero'd.
#endif

    //Initialize the Variance matrix Q.
    //1 meter x and y, and 1 degree heading.
    // ~ .31 meters per reading. * 10% is .0312
    m_Q(1,1) = aLON_PER_METER * .0312;
    m_Q(2,2) = aLAT_PER_METER * .0312;
    // heading variance
    m_Q(3,3) = DEG_TO_RAD * .25;

    //The GPS is accurate to a meter, but I don't really trust that.
    m_W(1,1) = aLON_PER_METER * 1.25;
    m_W(2,2) = aLAT_PER_METER * 1.25;
    //Compass is accurate to 4 degrees.
    m_W(3,3) = DEG_TO_RAD * 2.5;

    return aErrNone;

  } // stem is connected.

  else {
    return aErrConnection;
  }
	
  return aErrNone;
	
}

/////////////////////////////////////////////////////////////////////////////
void 
avcPosition::updateState(){
	// _updateStateWithDeadReckoningAccelEncoder();
	_updateStateWithDeadReckoningEncoderGps();
}


/////////////////////////////////////////////////////////////////////////////
void 
avcPosition::_updateStateWithDeadReckoningAccelEncoder() {
  //some statics for use in dead reckoning; these might be moved to the class
  static double integralAccelerationX=0.0, integralAccelerationY=0.0, integralAccelerationZ=0.0;
  //static double accelVelocityX=0.0, accelVelocityY=0.0, accelVelocityZ=0.0;
  static double accelLocationX=m_curPos.x, accelLocationY=m_curPos.y, accelLocationZ=0.0;
  static unsigned int integrationCount=0;
  
  double encoder_dx=0.0, encoder_dy=0.0; //encoder_vx=0.0, encoder_vy=0.0;
  double fDistRolled=0.0;// fVelocity=0.0;
  
  // get the change in time
  long unsigned int curClock;
	aIO_GetMSTicks(m_ioRef, &curClock, NULL);
	long unsigned int ticksElapsed = (curClock - m_curClock);
  double tmElapsed = ticksElapsed/1000.0;
  
  // get new encoder
  int curEnc = 0;
  if(!getEncoderValue(&curEnc)) {
		m_logger->log(ERROR, "%s: Encoder reading is fuct.", __FUNCTION__);
  }
  else {
    // calculate position change based on encoder
    fDistRolled =  m_metersPerTick * (double)(curEnc - m_Encoder);
    
    m_logger->log(INFO, "Encoder fDistRolled (m): %lf (tick/time=%d/%lf)", fDistRolled, (curEnc - m_Encoder), tmElapsed);
    
    // move the encoder distances into real-world frame using the previous bot heading
    encoder_dx = sin(m_curPos.h * DEG_TO_RAD)* fDistRolled * aLON_PER_METER;
    encoder_dy = cos(m_curPos.h * DEG_TO_RAD)* fDistRolled * aLAT_PER_METER;
    //encoder_vx = sin(m_curPos.h * DEG_TO_RAD)* fVelocity * aLON_PER_METER;
    //encoder_vy = cos(m_curPos.h * DEG_TO_RAD)* fVelocity * aLAT_PER_METER;
    
  } // endif getEncoderValue
  
  // grab the new compass heading
  // grab the current heading to enable observation of the change in heading
  float currentHeading = 0.0f;
  if(0 != m_pCompass->getHeadingDeg(&currentHeading)){
    m_logger->log(ERROR, "%s: Couldn't get new compass heading", __FUNCTION__);
  }
  
  // Store current readings (for the next predict phase)
  m_curPos.x += encoder_dx;
  m_curPos.y += encoder_dy;
  m_curPos.h = currentHeading;
  m_Encoder= curEnc;
  m_curClock = curClock;
  m_lastDistanceTraveled = fDistRolled;
  
  
  //////////////////////////////////////////////
  // pull in the accel data too
  //////////////////////////////////////////////
  double accelDeadReckoningScale = 0.0; // 1.0/2.5;
  if(accelDeadReckoningScale > 0.0){
    // grab the average accelerometer data
    double accX=0.0, accY=0.0, accZ=0.0;
    m_pAccelThread->getAverageAccerlerometerMeasurements(&accX, &accY, &accZ); // in bot frame
    
    // integrate current acceleration to velocity estimate and transform into real-world frame
    integralAccelerationX += tmElapsed * accX * sin(m_curPos.h * DEG_TO_RAD);
    integralAccelerationY += tmElapsed * accY * cos(m_curPos.h * DEG_TO_RAD);
    integralAccelerationZ += tmElapsed * accZ;

    // integrate previous velocity to new position
    accelLocationX += tmElapsed * integralAccelerationX;
    accelLocationY += tmElapsed * integralAccelerationY;
    accelLocationZ += tmElapsed * integralAccelerationZ;
    integrationCount++;
    
    // after a few cycles of dead reckoning with just the encoder,
    // calculate the difference in the accel-based and encoder-based position in bot-frame
    // do a weighted average of the two position estimates
    if(integrationCount > 5){
      double positionErrorX = accelLocationX - m_curPos.x;
      double positionErrorY = accelLocationY - m_curPos.y;
      m_logger->log(INFO, "Updating location based on accel errors: %lf, %lf", positionErrorX, positionErrorY);
      
      // weight the accel-based position with the encoder-based
      m_curPos.x += accelDeadReckoningScale * positionErrorX;
      m_curPos.y += accelDeadReckoningScale * positionErrorY;
      
      // reset the accel based location
      accelLocationX = m_curPos.x;
      accelLocationY = m_curPos.y;
      
      integrationCount=0; 
    }
	}
}

/////////////////////////////////////////////////////////////////////////////
void 
avcPosition::_updateStateWithDeadReckoningEncoderGps() {
	
	// Grab the clock. Use the aIO verison, clock is not accurate when 
	// we have stem processes running
	long unsigned int curClock;
	aIO_GetMSTicks(m_ioRef, &curClock, NULL);
	long unsigned int ticksElapsed = (curClock - m_curClock);
  double tmElapsed = ticksElapsed/1000.0;
	
	double encoder_dx=0.0, encoder_dy=0.0; //encoder_vx=0.0, encoder_vy=0.0;
  double fDistRolled=0.0;// fVelocity=0.0;
	
	// Check that we have actually had some time go by
  if(tmElapsed <= 0)
    m_logger->log(ERROR, "%s: Elapsed time is invalid", __FUNCTION__);
	
  // get new encoder
  int curEnc = 0;
  if(!getEncoderValue(&curEnc)) {
		m_logger->log(ERROR, "%s: Encoder reading is fuct.", __FUNCTION__);
  }
  else {
    // calculate position change based on encoder
    fDistRolled =  m_metersPerTick * (double)(curEnc - m_Encoder);
    
    m_logger->log(INFO, "Encoder fDistRolled (m): %lf (tick/time=%d/%lf)", fDistRolled, (curEnc - m_Encoder), tmElapsed);
    
    // move the encoder distances into real-world frame using the previous bot heading
    encoder_dx = sin(m_curPos.h * DEG_TO_RAD)* fDistRolled * aLON_PER_METER;
    encoder_dy = cos(m_curPos.h * DEG_TO_RAD)* fDistRolled * aLAT_PER_METER;
    
  } // endif getEncoderValue
	
	// grab the new compass heading
  // grab the current heading to enable observation of the change in heading
  float currentHeading = 0.0f;
  if(0 != m_pCompass->getHeadingDeg(&currentHeading)){
    m_logger->log(ERROR, "%s: Couldn't get new compass heading", __FUNCTION__);
  }
  
  // Store current readings (for the next predict phase)
  m_curPos.x += encoder_dx;
  m_curPos.y += encoder_dy;
  m_curPos.h = currentHeading;
  m_Encoder= curEnc;
  m_curClock = curClock;
  m_lastDistanceTraveled = fDistRolled;
	

  if(1){//(curEnc - m_Encoder) {
  	m_logger->log(INFO, "%s: --- fDist: %f", __FUNCTION__, fDistRolled);
    m_logger->log(INFO, "%s: --- hed: %f", __FUNCTION__, m_curPos.h);
  }
	
	m_logger->log(INFO, "%s: Set Integrate GPS State: ", __FUNCTION__);
	

#ifdef aUSE_GPS  
  //We really only want to use GPS information if enough time has passed.
	if ((curClock - m_gpsClock) > 500 && m_pGPS->getQuality()) {
		
		m_logger->log(INFO, "%s: Got good GPS quality");
		
    float curLon, curLat, curHed;
		
    //If we got any invalid BS, don't do this update.
    if(m_pGPS->getPosition(&curLon, &curLat, &curHed) == aErrNone) {
			
			// Now we do the error subtraction
			float errorLon = curLon - m_curPos.x;
			float errorLat = curLat - m_curPos.y;
			float errorHeading = curHed - m_curPos.h;
			
			// Only time GPS heading values are any good is when 
			// you are actually moving
			// We expect to be moving at a rate of 1/2 a meter a second
			// The we trust the compass is not lieing to us. If one of 
			// you fuckers are, we will rm -rf on your ass.
			if (tmElapsed && (fDistRolled / tmElapsed) > 0.5f) {
				errorHeading = 0.0f;
			}
			
			// Let's perform some crazy, arbitrary scaling values 
			// These will shape change our robots world. 
			m_curPos.x += m_fScalingErrorPosition * errorLon;
			m_curPos.y += m_fScalingErrorPosition * errorLat;
			m_curPos.h += m_fScalingErrorHeading * errorHeading;
			
			m_gpsClock = curClock;
    }
	}
#endif
	
}


/////////////////////////////////////////////////////////////////////////////
void 
avcPosition::_updateStateWithGpsEkf() {
	
	// Grab the clock. Use the aIO verison, clock is not accurate when 
	// we have stem processes running
	long unsigned int curClock;
	aIO_GetMSTicks(m_ioRef, &curClock, NULL);
	long unsigned int ticksElapsed = (curClock - m_curClock);
  double tmElapsed = ticksElapsed/1000.0;
	
	// First we must do an estimation step, given the previous position
  // and the current control information. Lets do this in meters, and then
	// convert to lat, lon.
	// We should be doing this step quickly enough that we can treat the movement
	// as linear.
	/*
	* x(k+1) = { cos(theta)fVel + x(k) } + vx(k)
	*	y(k+1) = { sin(theta)fVel + y(k) } + vy(k)
	* theta(k+1) = { dTheta + theta } + vtheta(k)
	* vx(k+1) = { cos(theta)fdist/T } + vVx(k)
	* vy(k+1) = { sin(theta)fdist/T } + vVy(k)
	* vtheta(k+1) = { dTheta/T }
	*/
	
	//Get the new encoder readings.
	int curEnc = 0;
	if(!getEncoderValue(&curEnc))
		m_logger->log(ERROR, "%s: Encoder reading is fuct.", __FUNCTION__);
  
	// Calculate the rear wheel velociy in meters / second.
  if(tmElapsed <= 0)
    m_logger->log(ERROR, "%s: Elapsed time is invalid", __FUNCTION__);
  
	
  double fVelocity =  m_metersPerTick * (double)(curEnc - m_Encoder) / tmElapsed;
  double fDistRolled =  m_metersPerTick * (double)(curEnc - m_Encoder);
  m_logger->log(INFO, "Current Speed (m/s): %lf (tick/time=%d/%lf)", fVelocity, (curEnc - m_Encoder), tmElapsed);
	
  // These calculations are predictions of where we think we need to be
  // estimate change in x and y and heading
  // TODO - we should use previous state vector to calculate position here.
  // previous velocity.
  double predicted_dx = sin(m_curPos.h * DEG_TO_RAD)* fDistRolled * aLON_PER_METER;
  double predicted_dy = cos(m_curPos.h * DEG_TO_RAD)* fDistRolled * aLAT_PER_METER;
    
  // Change in heading due to the previous steering angle
  double steerAngleRad = getSteeringAngleRad();
  double predicted_dh = fDistRolled/m_wheelBase * tan(steerAngleRad);
  
  // grab the current heading to enable observation of the change in heading
  float currentHeading = 0.0f;
  if(0 != m_pCompass->getHeadingDeg(&currentHeading)){
    m_logger->log(ERROR, "%s: Couldn't get new compass heading", __FUNCTION__);
  }
  
  // maybe use the change in heading from the compass to "predict" the change in heading
  //double predicted_dh = currentHeading - m_curPos.h;

  if(1){//(curEnc - m_Encoder) {
  	m_logger->log(INFO, "%s: --- fDist: %f", __FUNCTION__, fDistRolled);
    m_logger->log(INFO, "%s: --- dx(m): %f", __FUNCTION__, predicted_dx/aLON_PER_METER);
    m_logger->log(INFO, "%s: --- dy(m): %f", __FUNCTION__, predicted_dy/aLAT_PER_METER);
    m_logger->log(INFO, "%s: --- dh(m): %f", __FUNCTION__, predicted_dh);
    m_logger->log(INFO, "%s: --- hed: %f", __FUNCTION__, m_curPos.h);
  }
	// Store current readings (for the next predict phase)
  m_Encoder= curEnc;
  m_curClock = curClock;
	
  // Update the current control state vector
  // These vector values should be in latitude, longitude and degrees
//  m_curPos.x += dx;
//  m_curPos.y += dy;
//  m_curPos.h = currentHeading;
  m_lastDistanceTraveled = fDistRolled;
  
	Matrix state(3,1);
	//JLG flipped cos/sin - world cordinate system aligns latitude values with,
	//values along the x axis, and longitude values along the y axis.
	state(1,1) = m_curPos.x + predicted_dx;
	state(2,1) = m_curPos.y + predicted_dy;
	state(3,1) = m_curPos.h + predicted_dh;

  m_logger->log(INFO, "Set State: ");
	//EKF from here on out.
	//We need to calculate the probability matrix for the motion each time.
	Matrix F(3,3), G(3,3);
	
	//Setting diags for F to 1, and G 33 to 1.
	F(1,1) = F(2,2) = F(3,3) = 1;
	//Calculating the Linearization Matrix points for F.
	F(1,3) = -1.0*predicted_dx;
	F(2,3) = predicted_dy;
	
	//Calculate the Linearization Matrix points for G.
  // m_curPos.h is still the previous heading
	G(1,1) = tmElapsed*cos(m_curPos.h); 				G(1,2) = 0.0;
  G(2,1) = tmElapsed*sin(m_curPos.h); 				G(2,2) = 0.0;
  G(3,1) = tan(steerAngleRad)/m_wheelBase; 		G(3,2) = fDistRolled/(m_wheelBase * cos(steerAngleRad) * cos(steerAngleRad));
  m_logger->log(INFO, "Calculated F and G: ");
  
	//Now calculate the probability matrix for the position.
	m_P = F * m_P * F.transpose() + G * m_Q * G.transpose();
  
  m_logger->log(INFO, "Done m_P");

#ifdef aUSE_GPS  
  //We really only want to use GPS information if enough time has passed.
	if ((curClock - m_gpsClock) > 500 && m_pGPS->getQuality()) {
		m_logger->log(INFO, "here1");
    float curLon, curLat, curHed;
    //If we got any invalid BS, don't do this update.
    if(m_pGPS->getPosition(&curLon, &curLat, &curHed) == aErrNone) {
    	// We fall back to GPS heading here, we'll report an error.
      if(0 != m_pCompass->getHeadingDeg(&curHed))
        m_logger->log(INFO, "Error getting heading from compass");
		
      //Lets to this KF thing.
			Matrix V(3, 1);
			V(1,1) = curLon - state(1,1);
			V(2,1) = curLat - state(2,1);
			V(3,1) = curHed - state(3,1);
	  
      Matrix S(3, 3), R(3, 3);
      S = m_P + m_W;
      R = m_P * S.invert();
      state = state + R * V;
	  
	  	m_P = m_P - R * m_P;
	
			m_gpsClock = curClock;
    }
	}
#endif
	//Localization is done. Update the current robot state.
	m_curPos.x = state(1, 1);
	m_curPos.y = state(2, 1);
	m_curPos.h = state(3, 1);
	
	 
}

/////////////////////////////////////////////////////////////////////////////

#define		cmdMO_ENC32		66

bool 
avcPosition::getEncoderValue(int *pValue) {
	
	int value = 0;
  aUInt8 data[2] = {cmdMO_ENC32, 0};
  aPacketRef p = m_pStem->createPacket(aMOTO_MODULE, 2, data);
	int nAttemptsReadMax = 250;
	int nAttemptsWriteMax = 5;
	bool bValueGood = false;
	
	// Check the pointer is valid
	if (pValue == NULL) {
		return false;
	}
	
	// Otherwise we get to send off the read request
	do {
		// Send the request to the Moto
		m_pStem->sendPacket(p);
		
		// Begin polling over and over for the encoder 32 value
		do {
			
			// Delay
			m_pStem->sleep(1);
			
			// await the response packet
			acpPacket* pPacket = m_pStem->peekPacket(aMOTO_MODULE, cmdMO_ENC32);
			if (pPacket) {
				const aUInt8* pData = pPacket->getData();
				value = aUtil_RetrieveInt((const char*)&pData[2]);
				delete pPacket;
				
				// Value is good and get out of here
				bValueGood = true;
				
				break;
			}
		
		} while (nAttemptsReadMax--);
		
		
	} while (!bValueGood && nAttemptsWriteMax--);
	
	// Store the value
	*pValue = value;

	return bValueGood;
	
  //We could do more here to check for encoder wrap.
  //return m_pStem->MO_ENC32(aMOTO_MODULE, ENCODER_IDX);
  
}


/////////////////////////////////////////////////////////////////////////////
// Returns the steering angle in radians
double
avcPosition::getSteeringAngleRad(void) {

	//We could do more here to check for encoder wrap.
  // Cubic method.
	
	
	// Linear method.
  // Need to read the second byte, since the PAD_IO writes 2 bytes at a time
	unsigned char setpoint = m_pStem->PAD_IO(aSERVO_MODULE, AUTPAD_STEER+1);
	return (setpoint - SERVO_NEUT) * MAX_TURNANGLE / SERVO_NEUT;
	
}

/////////////////////////////////////////////////////////////////////////////
// Returns the motor set point (to be used to determine forward/backward driving
int
avcPosition::getMotorSetPoint(void) {
  
	// Linear method.
  // Need to read the second byte, since the PAD_IO writes 2 bytes at a time
	unsigned char setpoint = m_pStem->PAD_IO(aSERVO_MODULE, AUTPAD_THROT+1);
	return setpoint;
	
}

/////////////////////////////////////////////////////////////////////////////
// Accessor function for logging in controller; return the last distance traveled
// based on encoder tick delta
double avcPosition::getLastDistanceTraveled(){
  return m_lastDistanceTraveled;
}
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
int 
main(int argc, 
     const char* argv[]) 
{
  
  acpStem stem;
  aSettingFileRef settings;
  aErr e = aErrNone;
  aIOLib ioRef;
  
  // Grab an aIO reference object to gain the setting to talk to the stem.
  aIO_GetLibRef(&ioRef, &e);
  
  // Read from a settings file if it exists.
  if (aSettingFile_Create(ioRef, 
                          "chicken.config",
                          &settings,
                          &e))
    throw acpException(e, "creating settings");
  
  // or, maybe command line arguements
  aArguments_Separate(ioRef, settings, NULL, argc, argv);
  
  avcPosition position; 
  
  printf("connecting to stem\n");
  
  // This starts up the stem link processing and is called once to spawn
  // the link management thread... based on the settings.
  stem.startLinkThread(settings);
  
  // Wait until we have a solid heartbeat connection so we know there is 
  // someone to talk to.
  int timeout = 0;
  
  printf("awaiting heartbeat");
  
  do { 
    printf(".");
    fflush(stdout);
    aIO_MSSleep(ioRef, 500, NULL);
    ++timeout;
  } while (!stem.isConnected() && timeout < 30);
  
  printf("\n");
  
  // Bail if no stem. What's the point little man?
  if (timeout == 10) { return 1; }
	
	position.init(&stem, settings, avcWaypointVector(0,0,0));

//	for (int i = 0; i < 500; i++) {
  while (1){
    //float acc_x = 0, acc_y = 0, acc_z = 0;
		//printf("Compass reading: %f\n", position.getCHeading() * RAD_TO_DEG);
    printf("GPS Quality: %s\n", (position.getGPSQuality())? "good": "bad");
    printf("GPS sat count: %d\n", aGPM_GetSatellitesInUse(&stem));
    printf("GPS time: %d:%d:%d\n", aGPM_GetHours(&stem), aGPM_GetMinutes(&stem), aGPM_GetSeconds(&stem));
    printf("GPS date: %d-%d-%d\n", aGPM_GetYear(&stem), aGPM_GetMonth(&stem), aGPM_GetDay(&stem));
		
		aIO_MSSleep(ioRef, 200, NULL);
	}
  
  //printf("GPS Quality: %s\n", (position.getGPSQuality())? "good": "bad");
  
  aIO_MSSleep(ioRef, 1000, NULL);
  
  //////////////////////////////////
  // Clean up and get outta here. Run Forrest, RUN!!!
  aSettingFile_Destroy(ioRef, settings, NULL);
  aIO_ReleaseLibRef(ioRef, NULL);
  
  return 0;
  
}


#endif

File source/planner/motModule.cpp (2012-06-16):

///////////////////////////////////////////////////////////////////////////
// Filename: motModule.cpp

#include "motModule.h"

#ifdef aDEBUG_MOTMODULE
bool bDebugHeader = true;
#endif

///////////////////////////////////////////////////////////////////////////
// Constructor for the function
avcMotion::avcMotion() :
  m_pStem(NULL),
  m_settings(NULL),
  m_setpointMax(aMOTOR_SETPOINT_MAX),
  m_bInit(false),
  m_fThrottleWindow(aMOTMODULE_THROTTLE_WINDOW_DEFAULT)
{
  
  aErr e = aErrNone;
  
  // set up all the setpoint place holders
  for (int m = 0; m < aMOTOR_NUM; m++) {
    
    m_setpoint[m] = 0;
    m_setpointLast[m] = 0;
    
  }
  
  // Set the setpoint history to all neutral values
  for (int j = 0; j < aMOTMODULE_HISTORY_WINDOW; j++)
    m_setpointHistory[j] = SERVO_NEUT;
  
  // Create a aIO reference to manipulate settings file reference
  if(aIO_GetLibRef(&m_ioRef, &e)) 
    throw acpException(e, "Getting aIOLib reference");
  
}

///////////////////////////////////////////////////////////////////////////
// Destructor for the function
avcMotion::~avcMotion() 
{
  
  aErr e = aErrNone;
  
  if (aIO_ReleaseLibRef(m_ioRef, &e))
    throw acpException(e, "unable to destroy settings");
  
}

///////////////////////////////////////////////////////////////////////////
// Get the Stem object and initialize any thing else that we need to.

aErr
avcMotion::init(acpStem *pStem, aSettingFileRef settings) {
  
  // Get access to the logger class
  m_log = logger::getInstance();
  m_log->log(INFO, "Motion Module initialized");
  
  aErr e = aErrNone;
  
  // Grab the pointer to the Stem. 
  m_pStem = pStem;
  
  // Grab the pointer to the settings
  m_settings = settings;
  
  // Read motion module specific settings from the settings file
  // reference. Remember, this can get created from a configuration 
  // file, OR as command line input arguments. 
  int setpoint;
  aSettingFile_GetInt(m_ioRef, m_settings, 
		      aKEY_VELOCITY_SETPOINT_MAX,
		      &setpoint,
		      aMOTOR_SETPOINT_MAX,
		      &e);
  
  // Get the throttle max threshold as a percentage
  aSettingFile_GetFloat(m_ioRef, m_settings, 
                        aMOTMODULE_THROTTLE_WINDOW_KEY, &m_fThrottleWindow, 
                        aMOTMODULE_THROTTLE_WINDOW_DEFAULT, &e);
  
  // Boundary check the throttle window
  m_fThrottleWindow = m_fThrottleWindow < 0.0f ? 0.0f : m_fThrottleWindow;
  m_fThrottleWindow = m_fThrottleWindow > 1.0f ? 1.0f : m_fThrottleWindow;
  
  // Copy this into our member variable. Our setpoint is bounded by a 
  // 2 byte value. Short is enough. Likely even transition to an 
  // unsigned char since we are not likely to go past 200. 
  m_setpointMax = (short) setpoint;
  
  // We store and send the host side setpoint values into a scratchpad
  // A TEA process running on the servo module reads from this 
  // pad location and determines if it should use this or
  // do the manual override RC value.
  m_pStem->PAD_IO(aSERVO_MODULE, AUTPAD_THROT, SERVO_NEUT);
  m_pStem->PAD_IO(aSERVO_MODULE, AUTPAD_STEER, SERVO_NEUT);

  //m_log->log(INFO, "Read back steer pad %d",   m_pStem->PAD_IO(aSERVO_MODULE, AUTPAD_STEER+1))
  
  // Setting ramp configuration for the GP servo throttle setting
  // Where the second
  try {
    m_pStem->SRV_CFG(aSERVO_MODULE, THROT_SERVO, 
                     bitCMD_DEST_HOST | 0x81);
    m_pStem->SRV_CFG(aSERVO_MODULE, STEER_SERVO, 
                     bitCMD_DEST_HOST | 0x00);
  } catch (acpException &err) {
    m_log->log(ERROR, "%s: error writing ramp to GP", __FUNCTION__, err.msg());
  }
  
  // Read back the servo configuration from each servo motor
  unsigned char rampCheckThrottle = m_pStem->SRV_CFG(aSERVO_MODULE, THROT_SERVO);
  unsigned char rampCheckSteering = m_pStem->SRV_CFG(aSERVO_MODULE, STEER_SERVO);
  
  m_log->log(INFO, "Steering Servo Ramp: 0x%X", rampCheckSteering);
  m_log->log(INFO, "Throttle Servo Ramp: 0x%X", rampCheckThrottle);
  
  // Set the flag to inidicate that we have been properly initialized
  m_bInit = true;
  
  return e;
  
}

///////////////////////////////////////////////////////////////////////////
// Given a new goal Force vector, update the each motor setpoint
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

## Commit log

2011-02-11 Added CAD models for the Stems and a few sensors.
    [R323-ME-110.SLDPRT, R340-CMPS09.SLDPRT, S10-MOTO-BRD.SLDPRT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]
2011-02-12 Added Pittman gear motor
    [GM9234S022.SLDPRT]
2011-02-12 Added DS-CPMu file, HOKUYO laser, and exported all to IGS
    [DS-GPMu.IGS, DS-GPMu.SLDPRT, GM9234S022.IGS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]
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2011-02-13 Added a BOM for keeping track of extra purchases
    [BOM.xls]
2011-02-13 Added working files from BW's initial design
    [A 6H 3-34DF03710.SLDPRT, E4P-X-059-X-D-D-X.SLDPRT, Hub_threaded_side.SLDPRT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]
2011-02-14 updated files for 2010 compatibility
    [Side_Plate_Assembly.SLDASM, UAV_platform.SLDASM]
2011-02-14 Removed BOM and added debugging information to header file
    [BOM.xls]
2011-02-14 added itx
    [ITX_CPU.SLDPRT, Side_Plate_Assembly.SLDASM, Side_Plate_Assembly2.SLDASM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]
2011-02-14 Created models for power charging board.
    [BQ24703EVM.IGS, BQ24703EVM.SLDPRT]
2011-02-14 made 2010 version of the BQ24703EVM
    [BOM.xls, BQ24703EVM_2010.SLDPRT, Side_Plate_Assembly.SLDASM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]
2011-02-15 added directory for CNC files
    [UAV_platform.SLDASM, motor_plate.DXF, motor_plate.SLDDRW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]
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2011-02-16 Removed document
    [BOM.xls]
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2011-02-17 Added missing MO_SAV command and decreased the period on the motion channels to get better range with the test motors.
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2011-02-17 updated to add more ground clearance.
    [Half_Assembly.SLDASM, Left_Half_Assembly.SLDASM, Left_Side_Plate_Assembly.SLDASM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]
2011-02-18 updated main assembly and add cnc files
    [Left_Half_Assembly.SLDASM, Right_Half_Assembly.SLDASM, Side_Plate_Assembly4_no_motor.SLDASM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]
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2011-02-20 updated cnc files
    [Left_Half_Assembly.SLDASM, Left_Side_Plate_Assembly.SLDASM, Right_Half_Assembly.SLDASM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]
2011-02-21 4 motor modification
    [Left_Half_Assembly.SLDASM, Left_Side_Plate_Assembly.SLDASM, Right_Half_Assembly.SLDASM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]
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2011-02-27 updates CNC files and model with electronics plate
    [Left_Half_Assembly.SLDASM, Left_Side_Plate_Assembly.SLDASM, Right_Half_Assembly.SLDASM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]
2011-02-27 Adjusted makefile to build the whole project for Darwin or other OS (aka, Linux). Minor code fixes to planner.cpp and controller.cpp that were warnings treated as errors.
    [motModule.cpp]
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2011-03-01 Added missing global header file
    [avc2011.h]
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2011-03-10 added mini itx board.
    [miniITX.SLDPRT]
2011-03-10 added bracket for bottom electronics plate
    [Left_Half_Assembly.SLDASM, Left_Side_Plate_Assembly.SLDASM, Right_Half_Assembly.SLDASM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]
2011-03-10 Created IGES file of miniITX
    [miniITX.IGS]
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2011-03-14 fixed creation of logger object in planner.cpp
    [avc2011.h, locModule.cpp]
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2011-03-30 Have a limping robot. No more dead FETs. Lot's of blown fuses.
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2011-04-10 fixed typo in xml
    [locModule.cpp]
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2011-04-20 Fixed the sonar TEA code to handle scaling and multiple rangers
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2011-08-10 Added some files to help work on the pcb plate.
    [PCB_Plate.SLDPRT, PCB_Plate_Subsystem.SLDASM, SSW-118-01-G-S.SLDPRT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]
2011-08-11 started a bit of schematic capture
    [PCB_Plate.sch]
2011-08-11 A small bit of power inputs for motor side of things.
    [PCB_Plate.sch]
2011-08-12 Added current sensing to motor power line
    [PCB_Plate.sch]
2011-08-12 Added connector file for power connections. Could be the ONE.
    [MPT-08-01-01-X-RA-SD.igs]
2011-08-22 Added some samtec parts and a library file
    [PCB_Plate.sch]
2011-08-22 Adding lots of cad model work.
    [AR6115.SLDPRT, IPL1-110-01-X-D-RA.SLDPRT, MMSDT-10-24-M-END1.SLDPRT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]
2011-08-22 Added some missing cad files
    [Belkin_F7D1301v1.SLDPRT, Traxxas_EMAXX.SLDASM, Traxxas_EMAXX.SLDPRT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]
2011-08-29 Added rough dimension drawing of pcb
    [PCB_Plate.SLDPRT, PCB_Plate_Subsystem.SLDASM, Samtec-SSW-109-01-G-S.SLDPRT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]
2011-08-30 Started the board layout based on CAD model
    [PCB_Plate.brd]
2011-09-26 Added script file to create board dimensions from dxf.
    [PCB_Plate.brd, PCB_Plate.sch]
2011-10-03 PCB work. Tying things up, added mount holes to board layout. Loads more to do
    [PCB_Plate.brd, PCB_Plate.sch]
2011-10-04 More schematic capture. Assigned pin functionality on 20 pin header
    [PCB_Plate.brd, PCB_Plate.sch]
2011-10-10 Changing main 12.0V regulator to simple switcher
    [PCB_Plate.brd, PCB_Plate.sch]
2011-12-30 checking in switching regulator schematic capture
    [PCB_Plate.brd, PCB_Plate.sch]
2012-01-06 checking in minor pcb schematic changes. starting accel and gyro integration
    [PCB_Plate.brd, PCB_Plate.sch]
2012-01-07 Added generalized sensor interface
    [PCB_Plate.brd, PCB_Plate.sch]
2012-01-07 Added Garmin OEM module
    [PCB_Plate.brd, PCB_Plate.sch]
2012-01-09 added i2c a2d interface for a wider range of sensor inputs
    [PCB_Plate.brd, PCB_Plate.sch]
2012-01-09 added note about what accel to use
    [PCB_Plate.sch]
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2012-01-12 Checking in some routing on the pcb and added Devantech compass to the schematic
    [PCB_Plate.brd, PCB_Plate.sch]
2012-01-13 Minor routing to some LDOs
    [PCB_Plate.brd, PCB_Plate.sch]
2012-01-13 small bit more routing
    [PCB_Plate.brd]
2012-01-17 Mostly routed the switching regulator
    [PCB_Plate.brd, PCB_Plate.sch]
2012-01-21 added accelerometer and routed it
    [PCB_Plate.brd, PCB_Plate.sch]
2012-01-22 routed motor current measurement
    [PCB_Plate.brd, PCB_Plate.sch]
2012-01-22 moved connectors to mid plane of circuit board. jumpers for 20 pin connector are now together
    [PCB_Plate.brd]
2012-01-23 Started routing from 20 pin connector to patchbay
    [PCB_Plate.brd, PCB_Plate.sch]
2012-02-29 checking in plate routing for the square pcb. 10 airwires left
    [PCB_Plate_v6.brd, PCB_Plate_v6.sch]
2012-03-08 checking in a fully routed top plate. can one take any longer?
    [PCB_Plate_v6.brd, PCB_Plate_v6.sch]
2012-03-12 checking in board. revision a ready to go
    [PCB_Plate_v6.brd, PCB_Plate_v6.sch]
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2012-04-14 checking in schematic changes
    [PCB_Plate_v6.brd, PCB_Plate_v6.sch]
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2012-04-28 checking in motion module rework for 2012
    [avc2011.h, motModule.cpp]
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2012-05-04 - add map.track (example track only) - improved logging in planner - plannerTest now compiles - repulsiveTest verified with sensors - add IR sensor configs - improved logging in repulsiveForces - fix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
2012-05-09 fixed hacked servo motion code. now have command line throttle window as an option
    [motModule.cpp]
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2012-05-26 - add error check to getAccel in locModule - add gps
    [locModule.cpp]
2012-05-30 - fix GPS reading - move GetGPSQuality to gps.cpp - add reading of magnetometer pitch and roll in posTest - add gps to posTest - make posTest main a friend to location class
    [locModule.cpp]
2012-06-05 - slow down main loop for test logging clarity - enable GPS in locModule - fix? dx, dy calc in locModule - add logging in planner
    [locModule.cpp]
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2012-06-07 - fix scratch pad reading/writing confusions - fix lat/long mix in locModule - change to distance instead of velocity calcs to prevent rounding craziness - use #def for meter_per_tick in locMod insta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
    [locModule.cpp, motModule.cpp]
2012-06-08 - update chicken.config for testing - add test for CMPS10 - add factory cal reset for CMPS10 - fix main controller loop timer - enable compass in locModule - disable first GPS fix for testing - disab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
    [locModule.cpp, motModule.cpp]
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2012-06-10 - add loop delay and mapfile to chicken.config - move PlaySound to avc.h - remove voltage sound warning - switch to LSM303DLM compass - minor motionModule changes - flip y motivation from planner to 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
    [avc.h, locModule.cpp, motModule.cpp]
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2012-06-13 Updated ADXL335 accel to return m/sec^2 values and do running avg if wanted. Fixed uninitialized variable warning in lcoModule
    [locModule.cpp]
2012-06-13 - add accelerometer thread class - add hdop accessor to gps - add gps to locModule - fix build
    [locModule.cpp]
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2012-06-14 fixed 1 element arrays
    [locModule.cpp]
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2012-06-14 - add LSM303DLM.h - remove servo based +/- in locModule - correct ticks per meter with new encoder
    [avc.h, locModule.cpp]
2012-06-14 Updated error functionality in gps
    [locModule.cpp]
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2012-06-14 Fixed compiling warning cause I suck
    [locModule.cpp]
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2012-06-15 - update meters_per_tick based on second characterization - reposition repulsive force in controller (still disabled) - add getLastDistance traveled to planner and controller - fix plannerTest
    [avc.h, locModule.cpp]
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2012-06-15 - check in from late night work 2012Jun15 - update meters per tick for new encoder wheel - update locPlan logging to include a call to the compass - fix gps init in locModule - remove accel thread in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
    [avc.h, locModule.cpp]
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2012-06-16 - change max steer angle to 45 - change donut sizing - fix volume setting - fix locModule compile under optimization - fix motModule delta calc - fix planner for last point in map
    [avc.h, locModule.cpp, motModule.cpp]
2012-06-16 Fucking fixed all Justin's code. It goes to 11.
    [avc.h, locModule.cpp]
2012-06-16 added boolean to enable repulsive forces, and fixed the thread starting issues
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2012-06-16 - update chicken.config - update sparkFunLargeStep - enable repulsion by default (dumb config files and setting bools) - flip gps error logic (untested) - enable and tweak declination correction - tu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
    [locModule.cpp]
2012-06-17 - not tested in the field, but final code for 2012 - added repulse with long range (hack) - modified map (was tested, for first turn) - fix y-sign in planner adding of repulse and goal
    [repulsiveForces.h]
